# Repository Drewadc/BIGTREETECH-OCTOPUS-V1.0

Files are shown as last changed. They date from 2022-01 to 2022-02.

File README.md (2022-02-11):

This is a fork of the BTT Octopus firmware for the AnyCubic Chiron.  Details are in the sub folder, but I make no warranty or guarantee to this firmware.  It is what I use on my printer and may or may not be suitable for yours.  Use entirely at your own risk.  There are two versions of the firmware uploaded here.  One uses the stock AnyCubic display.  The other uses a BTT TFT35 E3 V3.0 (or equivalent I believe) display.

## BigTreeTech Octopus

### review
　You can find a complete review with detailed features of our electronics in [Spanish](https://3dwork.io/btt-octopus) and [English](https://3dwork.io/en/btt-octopus/) on [3dwork.io](https://3dwork.io/).

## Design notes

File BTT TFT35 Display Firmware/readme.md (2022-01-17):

The firmware.bin is a compiled version of the source code in the Marlin folder.  I STRONGLY recommend you compile your own so you know exactly what is setup.  I make no guarantee that this is fit for any purpose other than my own.

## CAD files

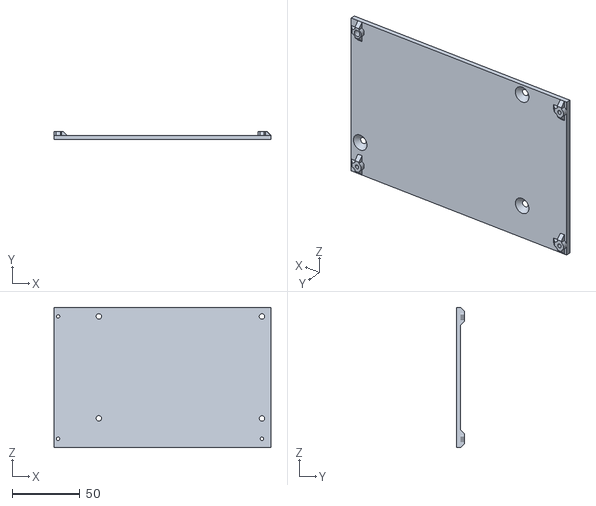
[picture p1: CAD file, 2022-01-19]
STL Files/OctopusChironPlate.stl
159.7 x 6.00 x 103.0

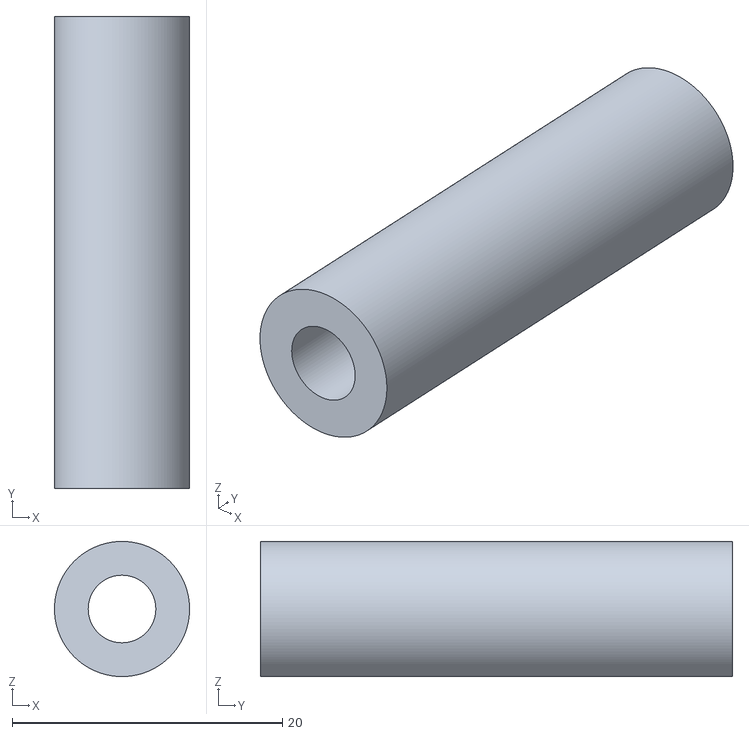
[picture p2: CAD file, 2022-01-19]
STL Files/OctopusChrionLongSpacer.stl
10.00 x 34.9 x 10.00

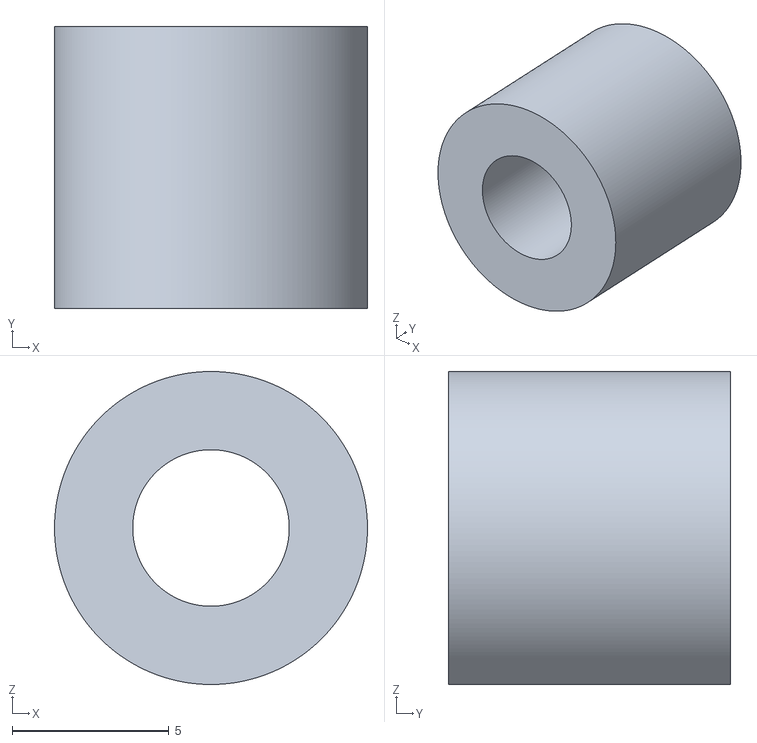
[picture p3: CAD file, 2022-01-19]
STL Files/OctopusChrionShortSpacer.stl
10.0 x 9.02 x 10.0

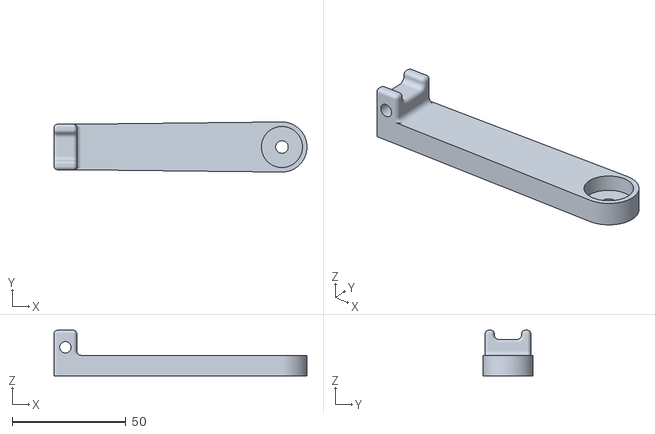
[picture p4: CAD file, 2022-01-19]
STL Files/ChrionStrainRelief.stl
111.0 x 22.0 x 20.0

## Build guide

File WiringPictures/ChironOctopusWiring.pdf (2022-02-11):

Note that all DIAG jumpers are removed since hardware endstops are used. Note that I had to change the pin order on at least one of the Z stops. The sensor ends of the cables are

# shown on the next page. X Stop

Y Stop

Z1 Stop
Z2 Stop

Filament

Runout

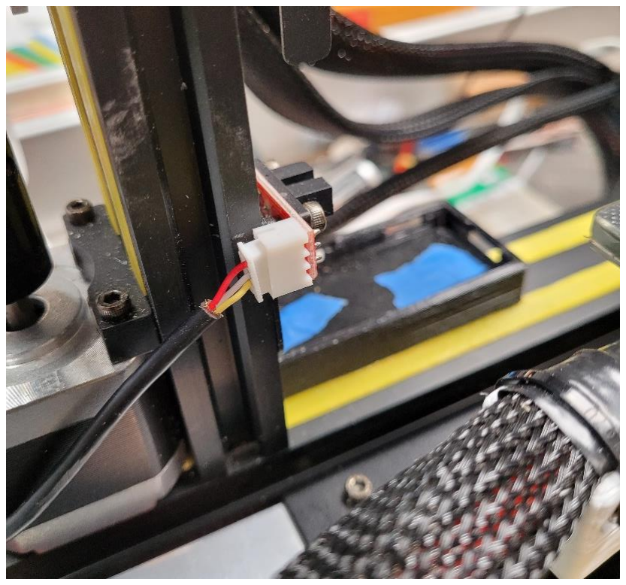
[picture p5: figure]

Z1 End Stop (Display/Extruder Side)

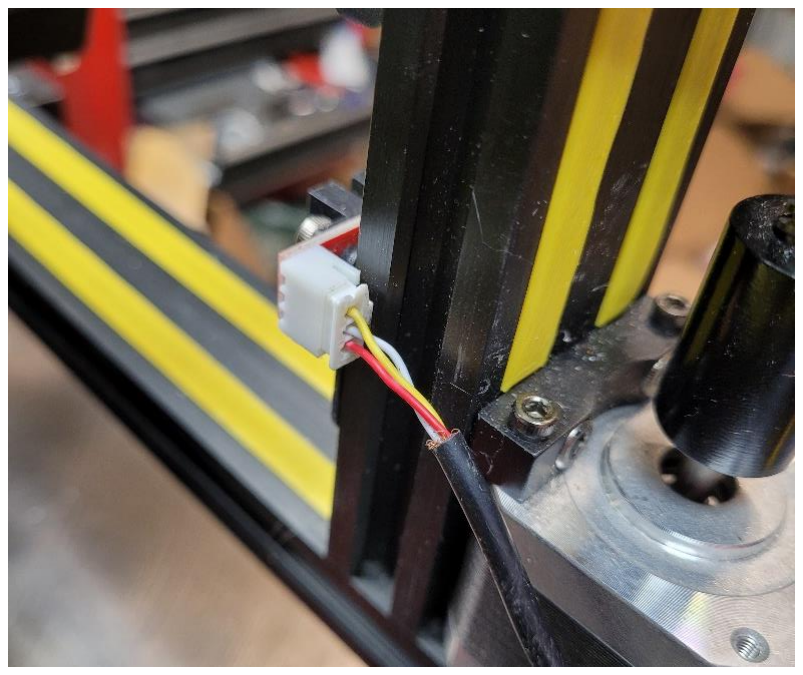
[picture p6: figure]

Z2 End Stop

Part Cooling Fan

Hotend Fan

Stepper Driver Fan

Hotend
Heater

The motor wire colors for my stepper motors likely don’t match stock as I used replacement cables that were longer and swapped pins to get rotation correct.

MOTOR0 | X
MOTOR1 | Y
MOTOR2_1 | Z 1
MOTOR2_2 | NOT USED
MOTOR3 | Z 2
MOTOR4 | E
X | Y | Z1 | Z2 | E

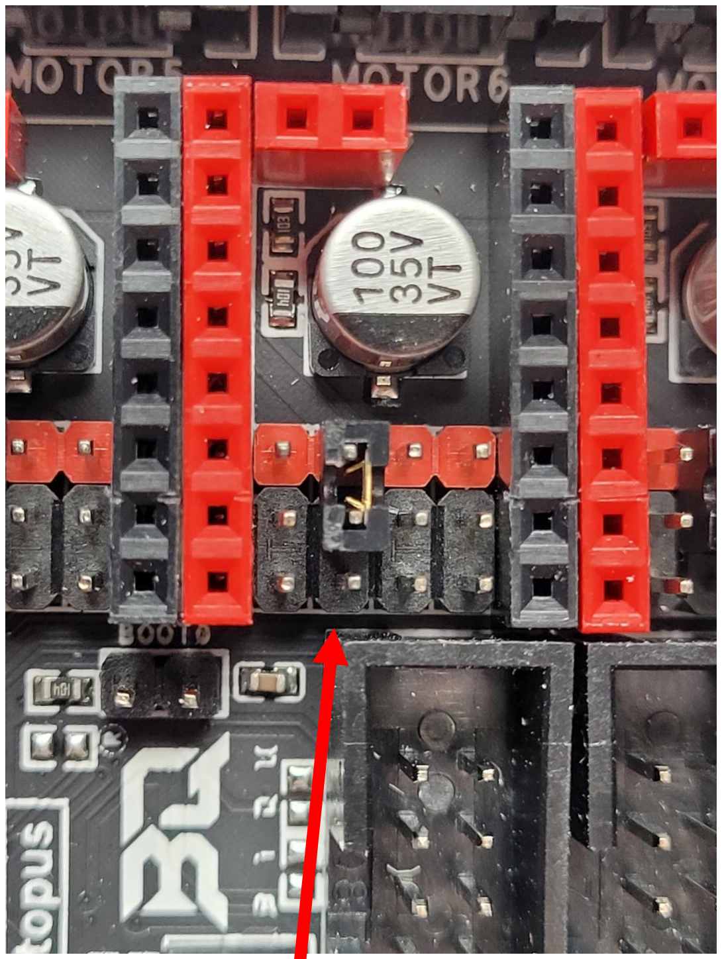
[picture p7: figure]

All stepper drivers (TMC2209) had the jumper shown installed to use the drivers in UART mode.

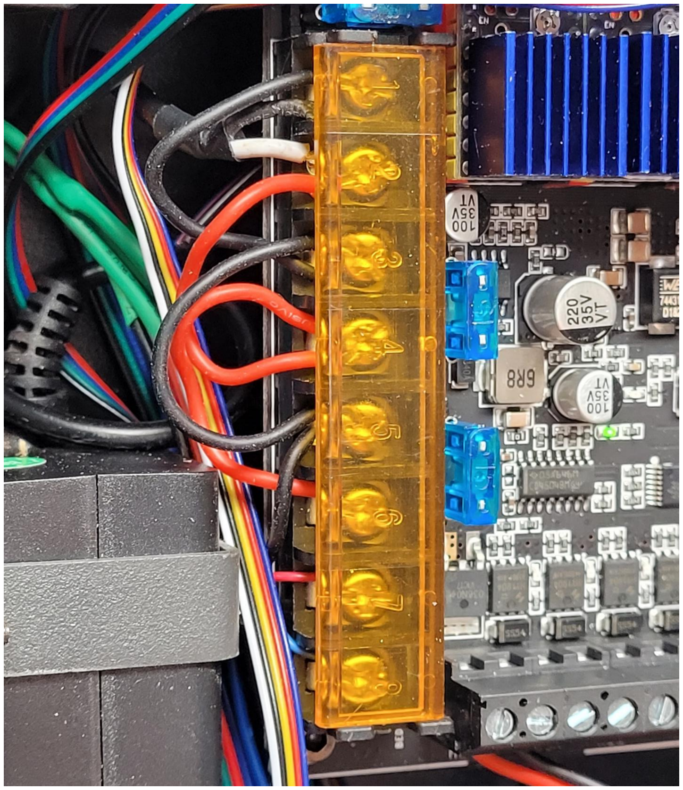
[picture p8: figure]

I ran all power input to the board from the small power supply and added jumper wires between the input terminals. I wired the MOSFET control wires into the Bed Out. I also ran a common neutral between the large and small power supplies.

I had to change the pin order on both my display cable and BL-Touch cable. Note that for the stock display, RX on the display connects to TX on the Octopus and TX on the display connects to RX on the Octopus. For the BTT TFT35 E3 V3.0, I did not have to swap RX and TX. For some BL-Touch/CR-Touch models, the cable supplied has the probe end wired in reverse order. The probe end of my cable is shown on the next page. If wires are in the wrong order, probability of damaging the probe or board is high.

BL

-Touch
Display

RST
TX (Display)
RX (Display)
Vss (GND)
5V

GND
5V
SERVO
GND
ZPROBE

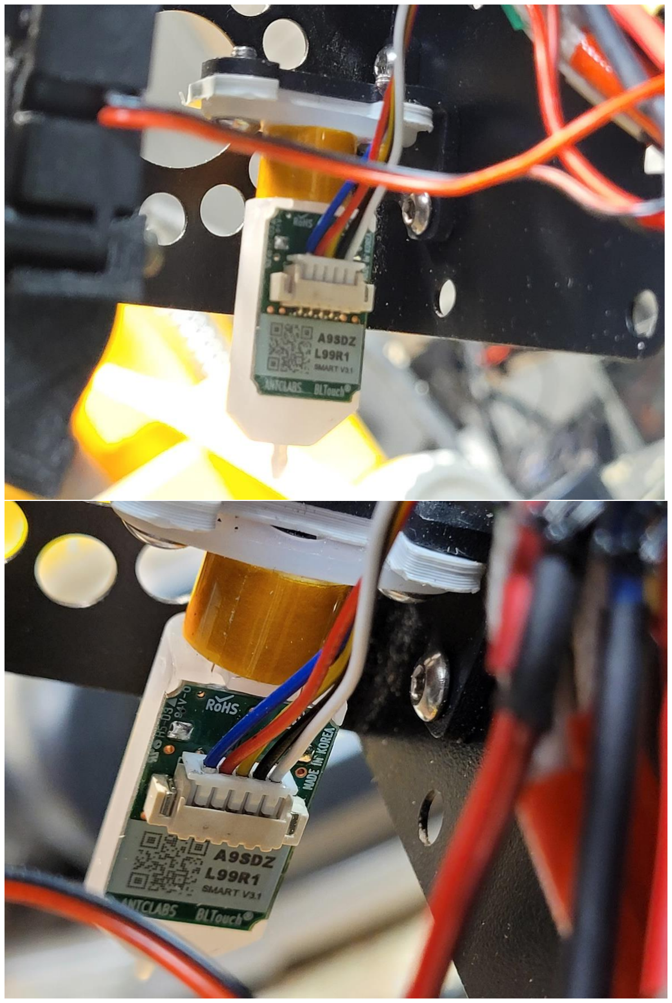
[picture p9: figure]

Bed Thermistor

Hotend Thermistor

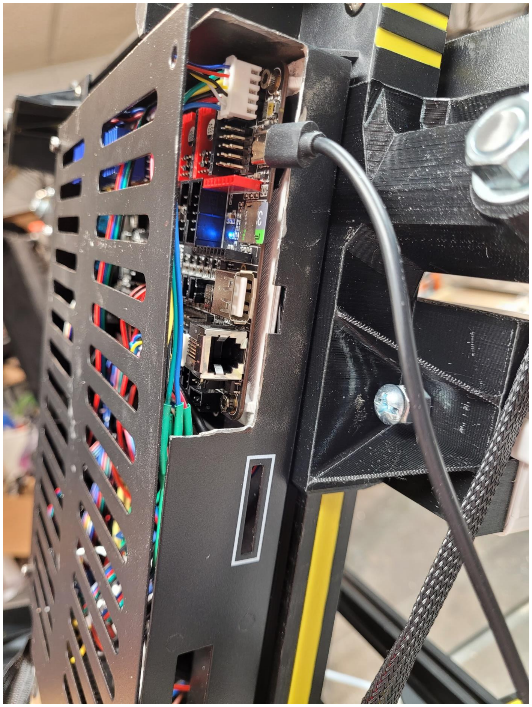
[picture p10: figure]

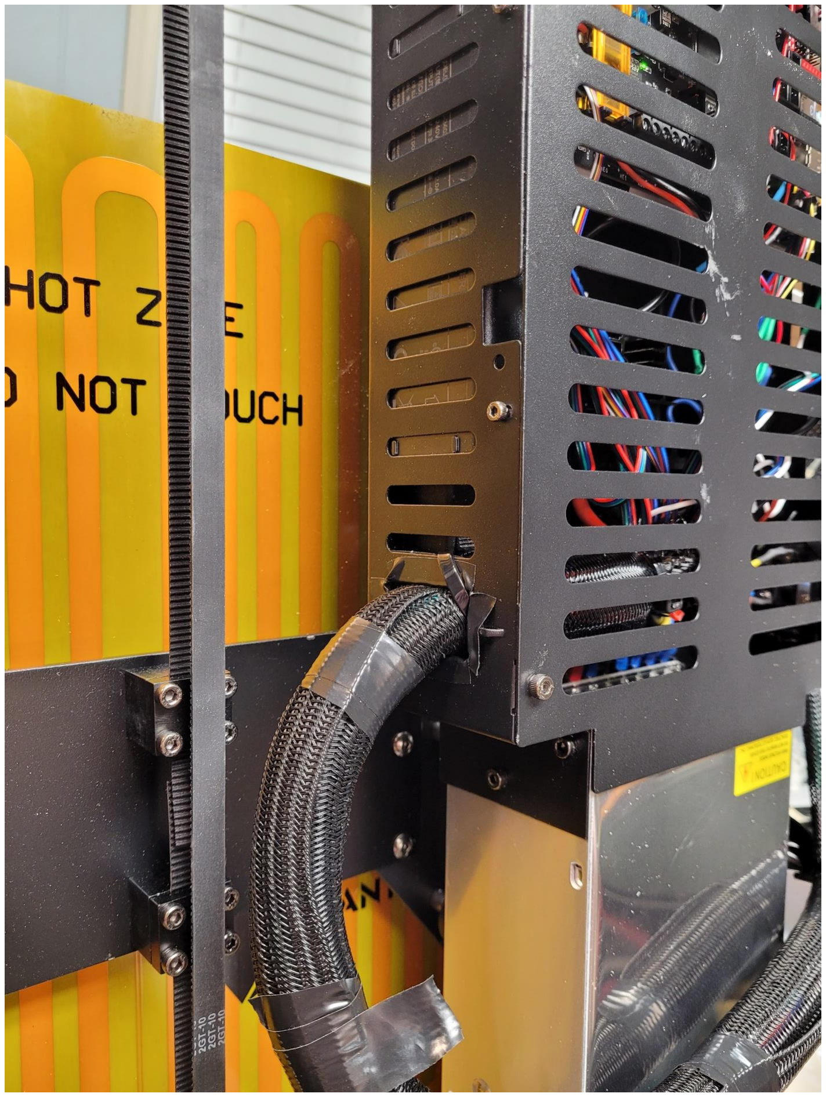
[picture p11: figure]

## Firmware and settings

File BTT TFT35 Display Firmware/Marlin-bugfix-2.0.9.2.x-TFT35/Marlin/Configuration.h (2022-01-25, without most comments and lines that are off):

#pragma once
#define CONFIGURATION_H_VERSION 02000903
#define STRING_CONFIG_H_AUTHOR "(BigTreeTech, Octopus)" // Who made the changes.
#define SHOW_BOOTSCREEN
#define SERIAL_PORT 2
#define BAUDRATE 250000
#define SERIAL_PORT_2 -1
#define SERIAL_PORT_3 1
  #define MOTHERBOARD BOARD_BTT_OCTOPUS_V1_1
#define CUSTOM_MACHINE_NAME "Anycubic Chiron"
#if LINEAR_AXES >= 4
  #define AXIS4_NAME 'A' // :['A', 'B', 'C', 'U', 'V', 'W']
#endif
#if LINEAR_AXES >= 5
  #define AXIS5_NAME 'B' // :['A', 'B', 'C', 'U', 'V', 'W']
#endif
#if LINEAR_AXES >= 6
  #define AXIS6_NAME 'C' // :['A', 'B', 'C', 'U', 'V', 'W']
#endif
#define EXTRUDERS 1
#define DEFAULT_NOMINAL_FILAMENT_DIA 1.75
#define TEMP_SENSOR_0 11
#define TEMP_SENSOR_1 0
#define TEMP_SENSOR_2 0
#define TEMP_SENSOR_3 0
#define TEMP_SENSOR_4 0
#define TEMP_SENSOR_5 0
#define TEMP_SENSOR_6 0
#define TEMP_SENSOR_7 0
#define TEMP_SENSOR_BED 1
#define TEMP_SENSOR_PROBE 0
#define TEMP_SENSOR_CHAMBER 0
#define TEMP_SENSOR_COOLER 0
#define TEMP_SENSOR_BOARD 0
#define TEMP_SENSOR_REDUNDANT 0
#define DUMMY_THERMISTOR_998_VALUE  25
#define DUMMY_THERMISTOR_999_VALUE 100
#define TEMP_RESIDENCY_TIME         10  // (seconds) Time to wait for hotend to "settle" in M109
#define TEMP_WINDOW                  1  // (°C) Temperature proximity for the "temperature reached" timer
#define TEMP_HYSTERESIS              3  // (°C) Temperature proximity considered "close enough" to the target
#define TEMP_BED_RESIDENCY_TIME     10  // (seconds) Time to wait for bed to "settle" in M190
#define TEMP_BED_WINDOW              1  // (°C) Temperature proximity for the "temperature reached" timer
#define TEMP_BED_HYSTERESIS          3  // (°C) Temperature proximity considered "close enough" to the target
#define TEMP_CHAMBER_RESIDENCY_TIME 10  // (seconds) Time to wait for chamber to "settle" in M191
#define TEMP_CHAMBER_WINDOW          1  // (°C) Temperature proximity for the "temperature reached" timer
#define TEMP_CHAMBER_HYSTERESIS      3  // (°C) Temperature proximity considered "close enough" to the target
#if TEMP_SENSOR_REDUNDANT
  #define TEMP_SENSOR_REDUNDANT_SOURCE    E1  // The sensor that will provide the redundant reading.
  #define TEMP_SENSOR_REDUNDANT_TARGET    E0  // The sensor that we are providing a redundant reading for.
  #define TEMP_SENSOR_REDUNDANT_MAX_DIFF  10  // (°C) Temperature difference that will trigger a print abort.
#endif
#define HEATER_0_MINTEMP   5
#define HEATER_1_MINTEMP   5
#define HEATER_2_MINTEMP   5
#define HEATER_3_MINTEMP   5
#define HEATER_4_MINTEMP   5
#define HEATER_5_MINTEMP   5
#define HEATER_6_MINTEMP   5
#define HEATER_7_MINTEMP   5
#define BED_MINTEMP        5
#define CHAMBER_MINTEMP    5
#define HEATER_0_MAXTEMP 300
#define HEATER_1_MAXTEMP 275
#define HEATER_2_MAXTEMP 275
#define HEATER_3_MAXTEMP 275
#define HEATER_4_MAXTEMP 275
#define HEATER_5_MAXTEMP 275
#define HEATER_6_MAXTEMP 275
#define HEATER_7_MAXTEMP 275
#define BED_MAXTEMP      150
#define CHAMBER_MAXTEMP  60
#define HOTEND_OVERSHOOT 15   // (°C) Forbid temperatures over MAXTEMP - OVERSHOOT
#define BED_OVERSHOOT    10   // (°C) Forbid temperatures over MAXTEMP - OVERSHOOT
#define COOLER_OVERSHOOT  2   // (°C) Forbid temperatures closer than OVERSHOOT
#define PIDTEMP
#define BANG_MAX 255     // Limits current to nozzle while in bang-bang mode; 255=full current
#define PID_MAX BANG_MAX // Limits current to nozzle while PID is active (see PID_FUNCTIONAL_RANGE below); 255=full current
#define PID_K1 0.95      // Smoothing factor within any PID loop
    #define DEFAULT_Kp  14.51
    #define DEFAULT_Ki   0.86
    #define DEFAULT_Kd  60.97
#define PIDTEMPBED
#define MAX_BED_POWER 255 // limits duty cycle to bed; 255=full current
  #define DEFAULT_bedKp 83.15
  #define DEFAULT_bedKi 11.78
  #define DEFAULT_bedKd 146.74
#define MAX_CHAMBER_POWER 255 // limits duty cycle to chamber heater; 255=full current
  #define PID_FUNCTIONAL_RANGE 10 // If the temperature difference between the target temperature and the actual temperature
#define PREVENT_COLD_EXTRUSION
#define EXTRUDE_MINTEMP 170
#define PREVENT_LENGTHY_EXTRUDE
#define EXTRUDE_MAXLENGTH 700
#define THERMAL_PROTECTION_HOTENDS // Enable thermal protection for all extruders
#define THERMAL_PROTECTION_BED     // Enable thermal protection for the heated bed
#define THERMAL_PROTECTION_CHAMBER // Enable thermal protection for the heated chamber
#define THERMAL_PROTECTION_COOLER  // Enable thermal protection for the laser cooling
#define USE_XMIN_PLUG
#define USE_YMIN_PLUG
#define USE_ZMIN_PLUG
#define USE_ZMAX_PLUG
#define ENDSTOPPULLUPS
#define X_MIN_ENDSTOP_INVERTING true // Set to true to invert the logic of the endstop.
#define Y_MIN_ENDSTOP_INVERTING true // Set to true to invert the logic of the endstop.
#define Z_MIN_ENDSTOP_INVERTING false // Set to true to invert the logic of the endstop.
#define I_MIN_ENDSTOP_INVERTING false // Set to true to invert the logic of the endstop.
#define J_MIN_ENDSTOP_INVERTING false // Set to true to invert the logic of the endstop.
#define K_MIN_ENDSTOP_INVERTING false // Set to true to invert the logic of the endstop.
#define X_MAX_ENDSTOP_INVERTING true // Set to true to invert the logic of the endstop.
#define Y_MAX_ENDSTOP_INVERTING true // Set to true to invert the logic of the endstop.
#define Z_MAX_ENDSTOP_INVERTING false // Set to true to invert the logic of the endstop.
#define I_MAX_ENDSTOP_INVERTING false // Set to true to invert the logic of the endstop.
#define J_MAX_ENDSTOP_INVERTING false // Set to true to invert the logic of the endstop.
#define K_MAX_ENDSTOP_INVERTING false // Set to true to invert the logic of the endstop.
#define Z_MIN_PROBE_ENDSTOP_INVERTING false // Set to true to invert the logic of the probe.
#define X_DRIVER_TYPE  TMC2209
#define Y_DRIVER_TYPE  TMC2209
#define Z_DRIVER_TYPE  TMC2209
#define Z2_DRIVER_TYPE TMC2209
#define E0_DRIVER_TYPE TMC2209
#define DEFAULT_AXIS_STEPS_PER_UNIT   { 80, 100, 400, 423 }
#define DEFAULT_MAX_FEEDRATE          { 200, 200, 25, 25 }
#define DEFAULT_MAX_ACCELERATION      { 3000, 3000, 100, 10000 }
#define DEFAULT_ACCELERATION          1500    // X, Y, Z and E acceleration for printing moves
#define DEFAULT_RETRACT_ACCELERATION  3000    // E acceleration for retracts
#define DEFAULT_TRAVEL_ACCELERATION   1500    // X, Y, Z acceleration for travel (non printing) moves
#define DEFAULT_EJERK    5.0  // May be used by Linear Advance
  #define JUNCTION_DEVIATION_MM 0.028 // (mm) Distance from real junction edge
  #define JD_HANDLE_SMALL_SEGMENTS    // Use curvature estimation instead of just the junction angle
#define BLTOUCH
#define NOZZLE_TO_PROBE_OFFSET { -25, -25, -1.95 }
#define PROBING_MARGIN 20
#define XY_PROBE_FEEDRATE (133*60)
#define Z_PROBE_FEEDRATE_FAST (4*60)
#define Z_PROBE_FEEDRATE_SLOW (Z_PROBE_FEEDRATE_FAST / 4)
#define MULTIPLE_PROBING 2
#define Z_CLEARANCE_DEPLOY_PROBE   10 // Z Clearance for Deploy/Stow
#define Z_CLEARANCE_BETWEEN_PROBES  8 // Z Clearance between probe points
#define Z_CLEARANCE_MULTI_PROBE     5 // Z Clearance between multiple probes
#define Z_PROBE_LOW_POINT          -10 // Farthest distance below the trigger-point to go before stopping
#define Z_PROBE_OFFSET_RANGE_MIN -30
#define Z_PROBE_OFFSET_RANGE_MAX 10
#define Z_MIN_PROBE_REPEATABILITY_TEST
#define X_ENABLE_ON 0
#define Y_ENABLE_ON 0
#define Z_ENABLE_ON 0
#define E_ENABLE_ON 0 // For all extruders
#define DISABLE_X false
#define DISABLE_Y false
#define DISABLE_Z false
#define DISABLE_E false             // Disable the extruder when not stepping
#define DISABLE_INACTIVE_EXTRUDER   // Keep only the active extruder enabled
#define INVERT_X_DIR false
#define INVERT_Y_DIR false
#define INVERT_Z_DIR false
#define INVERT_Z2_DIR false
#define INVERT_E0_DIR true
#define INVERT_E1_DIR false
#define INVERT_E2_DIR false
#define INVERT_E3_DIR false
#define INVERT_E4_DIR false
#define INVERT_E5_DIR false
#define INVERT_E6_DIR false
#define INVERT_E7_DIR false
#define X_HOME_DIR -1
#define Y_HOME_DIR -1
#define Z_HOME_DIR -1
#define X_BED_SIZE 400
#define Y_BED_SIZE 400
#define X_MIN_POS -10
#define Y_MIN_POS 0
#define Z_MIN_POS 0
#define X_MAX_POS X_BED_SIZE+10
#define Y_MAX_POS Y_BED_SIZE+10
#define Z_MAX_POS 455
#define MIN_SOFTWARE_ENDSTOPS
  #define MIN_SOFTWARE_ENDSTOP_X
  #define MIN_SOFTWARE_ENDSTOP_Y
  #define MIN_SOFTWARE_ENDSTOP_I
  #define MIN_SOFTWARE_ENDSTOP_J
  #define MIN_SOFTWARE_ENDSTOP_K
#define MAX_SOFTWARE_ENDSTOPS
  #define MAX_SOFTWARE_ENDSTOP_X
  #define MAX_SOFTWARE_ENDSTOP_Y
  #define MAX_SOFTWARE_ENDSTOP_Z
  #define MAX_SOFTWARE_ENDSTOP_I
  #define MAX_SOFTWARE_ENDSTOP_J
  #define MAX_SOFTWARE_ENDSTOP_K
#define FILAMENT_RUNOUT_SENSOR
  #define FIL_RUNOUT_ENABLED_DEFAULT true // Enable the sensor on startup. Override with M412 followed by M500.
  #define NUM_RUNOUT_SENSORS   1          // Number of sensors, up to one per extruder. Define a FIL_RUNOUT#_PIN for each.
  #define FIL_RUNOUT_STATE     HIGH        // Pin state indicating that filament is NOT present.
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

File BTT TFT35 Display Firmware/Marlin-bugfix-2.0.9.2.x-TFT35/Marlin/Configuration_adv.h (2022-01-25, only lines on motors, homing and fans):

  #define CONTROLLER_FAN_PIN FAN5_PIN           // Set a custom pin for the controller fan
#define E0_AUTO_FAN_PIN FAN4_PIN
#define E1_AUTO_FAN_PIN -1
#define E2_AUTO_FAN_PIN -1
#define E3_AUTO_FAN_PIN -1
#define E4_AUTO_FAN_PIN -1
#define E5_AUTO_FAN_PIN -1
#define E6_AUTO_FAN_PIN -1
#define E7_AUTO_FAN_PIN -1
#define CHAMBER_AUTO_FAN_PIN -1
#define COOLER_AUTO_FAN_PIN -1
#define COOLER_FAN_PIN -1
#define HOMING_BUMP_MM      { 5, 5, 2 }       // (mm) Backoff from endstops after first bump
#define HOMING_BUMP_DIVISOR { 2, 2, 4 }       // Re-Bump Speed Divisor (Divides the Homing Feedrate)
#define QUICK_HOME                          // If G28 contains XY do a diagonal move first
  #define HOME_AFTER_G34
#define MICROSTEP_MODES { 16, 16, 16, 16, 16, 16 } // [1,2,4,8,16]
  #define BABYSTEP_WITHOUT_HOMING
#define LIN_ADVANCE
  #define LIN_ADVANCE_K 0.05    // Unit: mm compression per 1mm/s extruder speed
#define ADVANCED_PAUSE_FEATURE
  #define ADVANCED_PAUSE_CONTINUOUS_PURGE       // Purge continuously up to the purge length until interrupted.
  #define ADVANCED_PAUSE_PURGE_FEEDRATE        5  // (mm/s) Extrude feedrate (after loading). Should be slower than load feedrate.
  #define ADVANCED_PAUSE_PURGE_LENGTH         50  // (mm) Length to extrude after loading.
  #define ADVANCED_PAUSE_RESUME_PRIME          0  // (mm) Extra distance to prime nozzle after returning from park.
  #define ADVANCED_PAUSE_FANS_PAUSE             // Turn off print-cooling fans while the machine is paused.
  #define HOME_BEFORE_FILAMENT_CHANGE           // If needed, home before parking for filament change
    #define X_CURRENT       800        // (mA) RMS current. Multiply by 1.414 for peak current.
    #define X_CURRENT_HOME  X_CURRENT  // (mA) RMS current for sensorless homing
    #define X_MICROSTEPS     16        // 0..256
    #define Y_CURRENT       800
    #define Y_CURRENT_HOME  Y_CURRENT
    #define Y_MICROSTEPS     16
    #define Z_CURRENT       800
    #define Z_CURRENT_HOME  Z_CURRENT
    #define Z_MICROSTEPS     16
    #define Z2_CURRENT      800
    #define Z2_CURRENT_HOME Z2_CURRENT
    #define Z2_MICROSTEPS    Z_MICROSTEPS
    #define E0_CURRENT      800
    #define E0_MICROSTEPS    16
    #define CURRENT_STEP_DOWN     50  // [mA]
    #define REPORT_CURRENT_CHANGE
  #define X_HYBRID_THRESHOLD     100  // [mm/s]
  #define X2_HYBRID_THRESHOLD    100
  #define Y_HYBRID_THRESHOLD     100
  #define Y2_HYBRID_THRESHOLD    100
  #define Z_HYBRID_THRESHOLD       3
  #define Z2_HYBRID_THRESHOLD      3
  #define Z3_HYBRID_THRESHOLD      3
  #define Z4_HYBRID_THRESHOLD      3
  #define I_HYBRID_THRESHOLD       3
  #define J_HYBRID_THRESHOLD       3
  #define K_HYBRID_THRESHOLD       3
  #define E0_HYBRID_THRESHOLD     30
  #define E1_HYBRID_THRESHOLD     30
  #define E2_HYBRID_THRESHOLD     30
  #define E3_HYBRID_THRESHOLD     30
  #define E4_HYBRID_THRESHOLD     30
  #define E5_HYBRID_THRESHOLD     30
  #define E6_HYBRID_THRESHOLD     30
  #define E7_HYBRID_THRESHOLD     30

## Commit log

2022-01-19 Redundant unnecessary files removed
    [BTT_OctoPus_Voron2_Config.cfg, Configuration.h, Memory usage.ods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]
2022-01-19 Add supplementary information
    Add wiring pictures.
    Add STL files of the mount used to put the BTT Octopus in the stock case.
    Add STL files of a bed cable strain relief I used when rewiring the printer.
    [ChrionStrainRelief.stl, OctopusChironPlate.stl, OctopusChrionLongSpacer.stl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]
2022-01-19 Update ChironOctopusWiring.pdf
    Add clarification that I had to swap connector pins in several locations.
2022-01-25 Change name to reflect stock display
    [Configuration.h, Configuration_adv.h, esp32.csv]
2022-01-25 Switch display to BTT TFT35
    Changed display to BTT TFT35. Should work with other serial displays also. Baud set to 250000. Note that 12864 emulation has not been tested yet via the EXP1 and EXP2 ports, but should be enabled in 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
    [Configuration.h, Configuration_adv.h, esp32.csv]
2022-02-11 Update ChironOctopusWiring.pdf
    Add pictures of Z stop sensor and Z probe ends of cables.

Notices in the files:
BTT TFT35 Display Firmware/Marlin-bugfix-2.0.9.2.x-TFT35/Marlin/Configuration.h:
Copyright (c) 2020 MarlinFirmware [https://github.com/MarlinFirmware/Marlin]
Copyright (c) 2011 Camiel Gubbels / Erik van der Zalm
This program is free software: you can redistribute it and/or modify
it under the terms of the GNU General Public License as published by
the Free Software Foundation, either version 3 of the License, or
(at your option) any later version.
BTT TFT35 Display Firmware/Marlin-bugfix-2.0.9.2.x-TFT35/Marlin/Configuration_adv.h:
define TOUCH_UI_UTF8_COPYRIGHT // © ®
